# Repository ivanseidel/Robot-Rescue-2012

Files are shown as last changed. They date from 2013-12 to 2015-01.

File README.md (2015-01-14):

Robot-Rescue-2012
=================

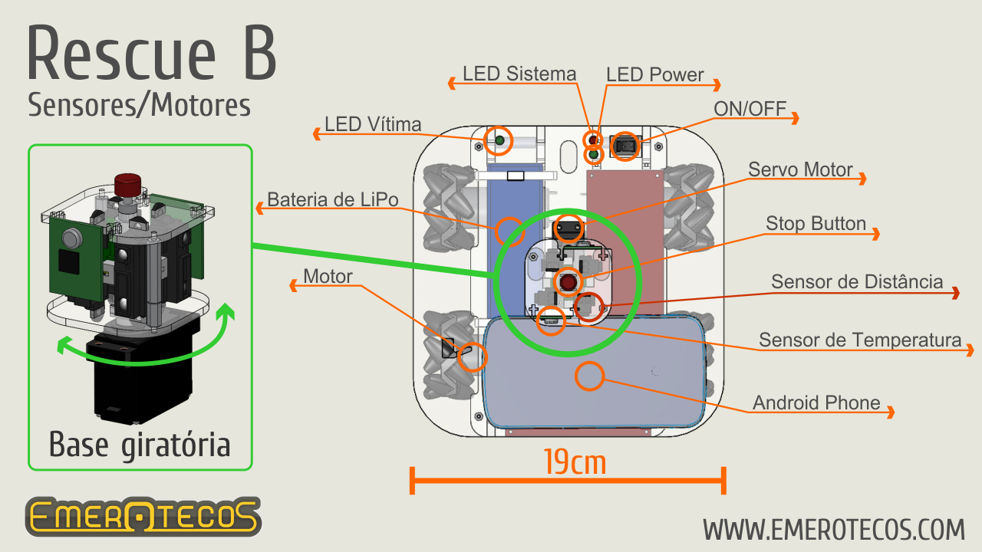
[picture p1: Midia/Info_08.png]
RoboCup Rescue B


This repository includes the entire Rescue B project from 2012, used in the international RoboCup Rescue B league.
Our team could acomplish the 3th place in super-team and 1st place of robot design.

There is a currently new version of it (on the picture, the 2013 one), find out more [here](https://github.com/ivanseidel/Robot-Rescue-2013).

This robot was the first Android based robot, that used the cellphone as the main processor and could controll the entirely the robot. We could acomplish heavy calculations using Android's 2.4Ghz processor, creating really "expensive" euristics.

The software has about 12.000 lines of code, written in Java, using Interfaces, and Classes hierarchy to provide well encapsulated code, and easy to use.

The image bellow is the sketch of the sensors/controllers.

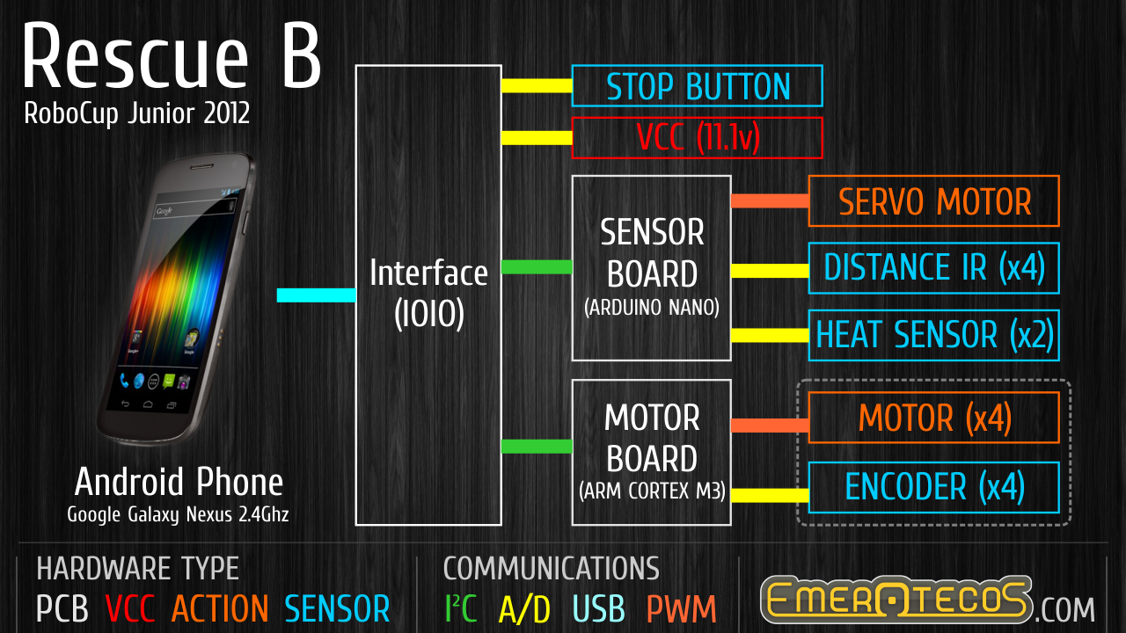
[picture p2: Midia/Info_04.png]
RoboCup Rescue B connections


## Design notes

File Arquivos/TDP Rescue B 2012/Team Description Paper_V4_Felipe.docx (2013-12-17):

[^1]

# Team Description Paper: Team Emerotecos

André Seidel Oliveira¹, Gabriel Lima Guimarães², Ivan Seidel Gomes³, Matheus Pimentel Canejo Pinheiro da Cunha⁴, Hudson Cássio Gomes Oliveira⁵, Felipe Nascimento Martins⁶

Abstract— This paper presents a description of an omnidirectional robot to be used on the Rescue B competition. The main robot controller was written in Java and runs in an Android-based mobile phone. The phone is connected to an IOIO board that serves as an interface between the main controller and the robot’s motors and sensors. The IOIO board connects to an Arduino board, that is responsible for the distance and temperature sensors readings, and to an MBed board that controls the motor drivers. There are four infra-red distance sensors mounted on a rotary base on the top of the robot. The base angle is constantly changed by a servomotor, which allows a 360º distance measuring. The robot mechanical structure was designed using a 3D modeling software and was built using acrylic. It has four omnidirectional wheels that allow the robot to move in any direction without the need of turning itself. The robot was entirely designed, built and programmed by the team students.

# I. Introduction

This is to show team Emerotecos’ strategies to solve the challenge proposed to the Rescue B Competition.

To build the robot, we didn’t use any building kit, as we designed the whole robot from sketch, using Dassault Systemes’ Solid Works software [1]. The robot was built basically with 5mm thick acrylic pieces, whose are tough enough for the application.

As the main processor, we use an Android phone, which is programmed using Java. This is a very interesting platform to work with since nowadays Android is the world’s most popular mobile platform [2].

To send the signals from the Android to the motors (that are controlled by an MBED board [3]), we use a board called IOIO, which is responsible for reading all the sensors as well [4].

# II. Objective

The objective of this project is to build a smart robot that can cross a maze build with wood walls, and identify the electrically heated victims that are placed along the maze’s walls.

# III. Ambient

The Challenge happens in a modular arena, made with wood, which has 2 floors, and 4 main rooms. The location of the walls are always unknown by the time the robot starts running, so that it runs in a real maze. The only constant information about the arena, is its total size, what makes it easier to the robot to find its way on the place. An illustration of the maze is shown in Figure 1.

Some heated “victims” are randomly positioned on some walls in the arena, and the robot has to identify them to get points.

In some places, there are some “dead ends”, which are a black mat on the ground. The robot can run over these black mats, but it has to leave it on the same side it came from, it can’t cross the black area.

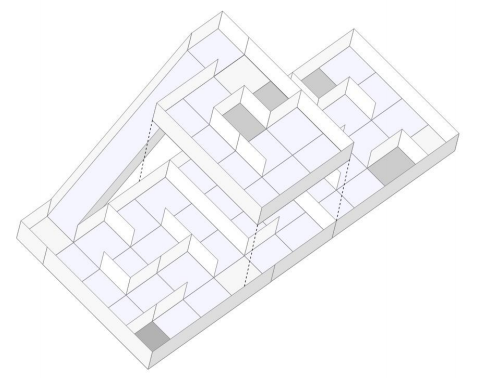
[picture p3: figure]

Figure 1.  Rescue B Arena illustration.

# IV. Strategy

## A. Robot Structure

Our robot is built basically with 2 acrylic layers, and some acrylic beams. We use a Mecanum omnidirectional wheels system, which makes our robot able to drive to every direction. The Mecanum system works as a regular omni system, but it uses 4 tractioned wheels, instead of three, normally used. Figure 2 shows the robot design and Figure 3 shows the actual robot, without the control boards.

We use 4 very strong motors, with encoders, so that we can precisely move our robot everywhere. We rely on 4 motors, one for each wheel, because the MECANUM omnidirectional system need dierent control for each wheel. Each motor can spin giving a 6kgm torque, and its encoder can read up to 3592 pulses per turn because we have a 75:1 speed reduction.

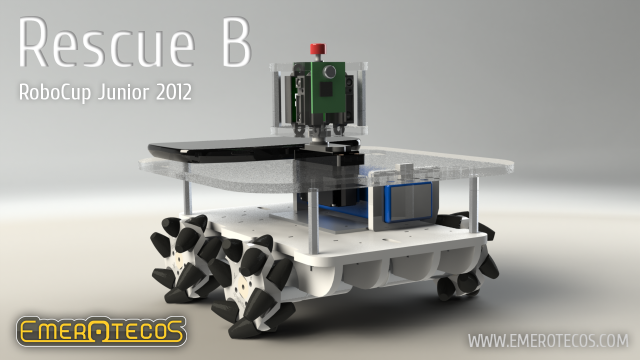
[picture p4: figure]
Info_05

Figure 1.  Robot design.

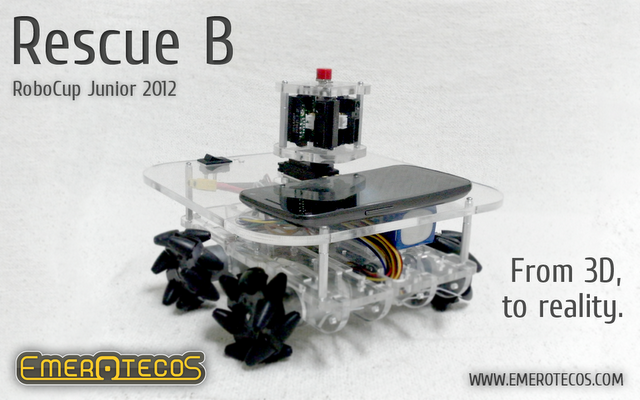
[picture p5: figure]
Info_06

Figure 2.  Robot picture(without control boards).

To process the encoder pulses, we have a MBED board, using a ARM Cortex M3, at 100MHz. This board is also responsible for controlling the engines speed. The communication protocol used to read the encoders from the interface, and to set the motors speeds, is the I²C. The MBED board only has 3 encoder inputs. So, we had to program another encoder counter.

To make good measurements with the infrared distance sensors, we’ve put them in a turnable head over the robot, so that we can make meausures to every direction. To identify the victims, we have 4 thermal infrared sensors strategically positioned around the robot, so that we can measure temperatures in every wall.

As we use complex algorithms (described latter), we need a very complex processing unit. For this reason we have decided to use an Android phone on our robot. Android because we can program using Java. Also, the phone has a touchscreen LCD screen and several sensors we can access. For instance, we make use of the 3 axles gyroscope and 3 axles magnetometer that are present on the Android phone. This gives the robot a very precise way to know it’s position and angle, on all axles.

As you can see in the Figures 2 and 3, the distance sensors are positioned on rotary base on the top of the robot. This base is driven by a servomotor so that the sensors can be aimed to virtually any direction. Its visible too how are the Mecanum wheels mounted on the robot, similar to a Four by Four car, but with the capacity of moving to any direction without the need to turn.

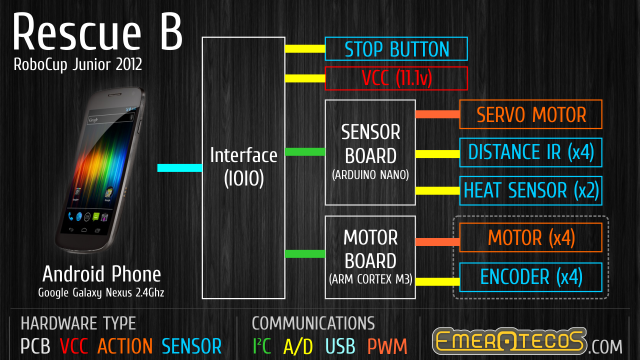
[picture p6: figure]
Info_04

Figure 3.  Control System overview.

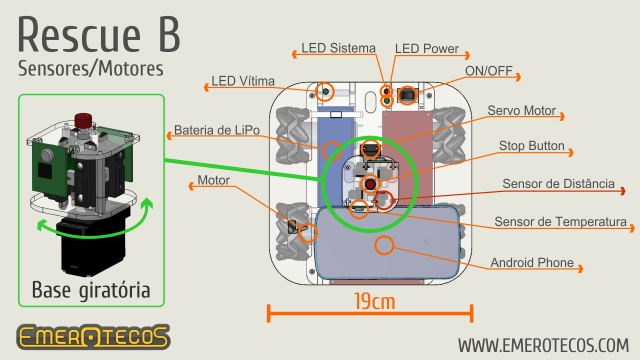
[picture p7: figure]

Figure 4.  Rotary base (left) and top view of the robot.

## B. Programming

The main controller of our robot is an Android cellphone. We choose Android, because it’s an open platform [2], and it’s possible to connect the cellphone with the sensors easily, using the IOIO board [4].

The Android phone sends and receives data to/from the IOIO, which reads the sensors, and communicates with the MBED board, the one responsible for controlling the motors. Figure 4 shows the control system overview.

Our robot uses 2 types of sensors: infrared distance sensor (by Sharp) and heat sensor. The heat sensor is used to detect the victims and are placed on the robot borders. As explained on the previous section, the infrared sensors are mounted on a rotary base. Each one of infrared sensors are pointed 90º from each other in a way that the 4 distance measures can be made at once. The 4 distance measures are repeated several times during a head rotation (one measure per degree) in order to detect the maze walls and obstacles. Figure 5 shows the rotary base with the infrared sensors placed on it, and presents a top view of the robot.

The distance measures are also used to correct the robot alignment in order to maintain its correct orientation parallel to the maze walls. This is done by comparing the measures at 20º and -20º from the central line, and calculating the necessary robot turning to make the robot alignment. Figure 6 illustrates the described idea.

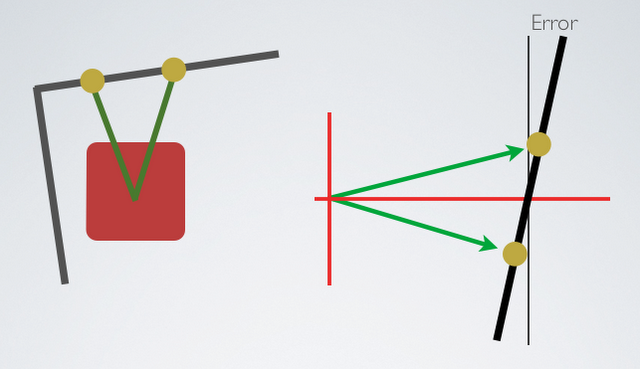
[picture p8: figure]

Figure 5.  Robot design.

To move the robot, we use a simplified kind of SLAM (Simultaneous Localization And Mapping) algorithm, so that we can map the arena. We know that the walls are oriented in only 2 directions (0º and 90º), and we also know that each part of the maze is formed by a 30 x 30 cm square. With this knowledge and using the distance measures obtained via the infrared sensors, we can find out the walls positions and build a map of the maze. The SLAM was programmed in JAVA, and it runs on the Android while the robot is moving in the arena.

While the robot walks around the arena, we can see the map being formed on the cellphone’s screen. Figure 6 shows an example of the mapping screen.

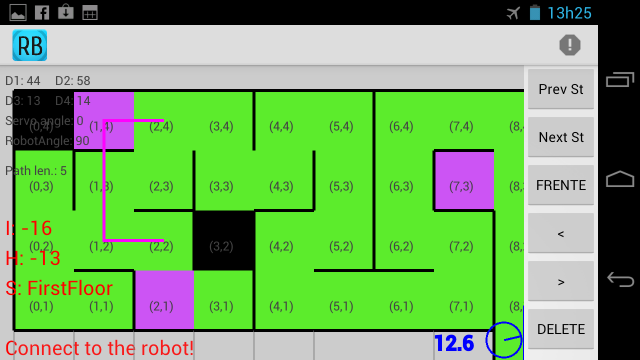
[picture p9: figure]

Figure 6.  On-line mapping.

# V. Conclusion

Mapping is the best way to solve this challenge, because it makes it easy to visit every module of the arena, and consequently, find all victims. We have successfully used this robot in the RoboCupJunior 2012 Rescue B competition. A presentation video about the robot is available in [5].

# VI. Acknowledgement

The authors thank the following companies for the financial support that allowed the robot construction and participation at the 2012 RoboCup and CBR competitions: Proesi Componentes Eletrônicos, Nova Didacta, InTechno Desenvolvimento e Capacitação, Copy Express, Produtiva Hailtools, Use Móveis para Escritórios and Qualidata. They also thank IFES for the support and FAPES (a foundation of the Secretary of Science and Technology of the State of Espirito Santo, Brazil) for the financial support to pay for the air tickets and travel expenses to Fortaleza – LARC 2012 (Project 57768773/2012).

# References

[1] 3D CAD Design Software SolidWorks. Available at: http://www.solidworks.com/. Access: Sep. 5, 2012.
[2] Andoid, the world’s most popular mobile platform. Available at: http://developer.android.com/about/index.html. Access: Sep. 5, 2012.
[3] Mbed - Rapid Prototyping for Microcontrollers. Available at: http://mbed.org/. Access: Sep. 5, 2012.
[4] IOIO Documentation. Available at: https://github.com/ytai/ioio/wiki. Access: Sep 5, 2012.
[5] NERA. Prêmio de Melhor Robô do mundo é de alunos do IFES! (com vídeo). Available at http://nera.sr.ifes.edu.br/?p=143. Access: Sep. 5, 2012.

[^1] The authors are with the Federal Institute of Education, Science and Technology of Espírito Santo (IFES). Rodovia ES-010, km 6,5 - Manguinhos, Serra, ES. andre_oliveira@live.com¹, gablg@hotmail.com², ivanseidel@gmail.com³, pimentelcanejo@hotmail.com⁴, hudsoncassio@ifes.edu.br⁵, felipemartins@ifes.edu.br⁶.

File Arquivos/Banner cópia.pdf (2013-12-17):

## The Problem

One of our biggest problems is to find all victims in the maze, the fastest way possible. As we don’t have to find the end of the maze, to find all victims, all we have to do is go everywhere in the maze.

## The Robot: Mechanics

This year, we said bye to the NXT brick, thanks to it’s weight, and to it’s engines size. We decided to build from sketch an entire robot, using 2 5mm acrylic layers and some acrylic beams under the structure to support the engines and the electronics. The MECANUM wheels, are just like an ordinary omnidirectional system, but with the wheel mounted in a different way.
We use a servo in the center of the robot, that is used to move the sensors, giving them a bigger reading area.
Our robot measures 200x200mm, which makes it possible for the robot to spin without touching the walls. We use 5mm acrylic, because we know (by tests) that it is tough enough. We cut it with laser (on CopyExpress) giving us a 0.01cm precision. All drawing have been made on SolidWorks!
We also used a 3D printer to do some parts on our robot, like the thermopile array`s stand.

## The Robot: Electronics

Yes, we use a cellphone! As we use very complex algorithms, we need a very complex processing unit, that’s why there is an Android phone on our robot. Android because we can program using java, without any problem, and we still have a LCD screen, and a touchscreen panel, with which we can make the initial configurations.
To fire up the engines, read the sensors, and control the engines position, we have, basically 2 PCB’s.
To feed the monster, we use a liPo battery, which gives us 11.1v, 65A, and is very lightweight.

### Interface

We have a interface that is responsible to connect the Android (via USB) to the robot. It`s called the IOIO board, which will communicate with the MBED, that will read the sensors and spin the wheels.

### Locomotion

We rely on 4 engines, one for each wheel, because the MECANUM omnidirectional system need different control for each wheel. Each engine can spin giving a 6kg torque, and can read up to 3592 pulses per turn of the final axle even though we have a 75:1 speed reduction.
To process all this pulses, we have a MBED board, using a ARM Cortex M3, at 100Mhz speed. That board is also responsible for controlling the engines speed. The protocol used to read the encoders from the interface, and to set the speeds, will be I2C Fast.
The MBED board have an onboard encoder counter for only 3 engines, fact that make us emulate another encoder counter (he hope NXP can read this, so that, on the next time, we won’t need to emulate the counter)

### Sensoring

The Algorithm we’re using needs a lot of distance measures around the robot. If one rotates 4 sensors for 90 degrees, one’ve got 360 degrees of pure distance measurement! And as we use 2 thermopiles arrays, one’ll have a 180 degrees of temperature measurement (more than enough).
The MBED is responsible for making the reading, filtering, and sending them via I2C!

### IMU

Besides all that sensors, we also have an 9 axles Inertial Measurement Unit (IMU). It’s basically an unit that joins a 3 axles gyroscope, a 3 axles accelerometer, and a 3 axles magnetometer, giving the robot a very precise way to know it’s position and angle, on all axles (we hope we are in a 3D world).

## The Robot: Software

We will do our best to find the victims the fastest we can. We’re used to write all the code in C, but this time, we are using C++ for the MBED and Java (and C++) for the Android. This year, we`re implementing a very complex algorithm, usually used in situations involving mazes. It`s called SLAM! (simultaneous localization and mapping). As you can see, the algorithm basically maps the arena, but in the same time, it locates the robot in the arena.

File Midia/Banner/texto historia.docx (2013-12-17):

O império Bizantino foi um império formado por várias nações da Eurásia como continuação do império Romano do Oriente durante o fim da Antiguidade Tardia e a Idade Média, a partir do século IV, depois da tomada do império Romano do Ocidente pelas invasões bárbaras.

A história desse império se inicia com a dinastia de Constantino I, que mudou a sede do Império para sua recem-fundada cidade Constantinopla no ano de 330. O principal motivo para essa mudança repentina foram os constantes ataques bárbaros ao lado Ocidental do Império Romano.

Sob o domínio de Constantino I, Roma teve grandes mudanças, sendo as principais a popularização do cristianismo e a valorização da moeda, que levou o Império a se tornar próspero novamente e, consequentemente, a re-estruturar seu exército.

O estado do império até os anos de 400 pode ser descrito em termos do resultado do trabalho de Constantino. O princípio dinástico foi estabelecido tão firmemente que o imperador que morreu naquele ano, Teodósio I, deixou o cargo imperial em conjunto para seus filhos: Arcádio no Oriente e Flávio Honório no Ocidente. Teodósio foi o último imperador a governar o Império Romano único.

O império do Oriente foi poupado das dificuldades enfrentadas pelo Ocidente nos séculos III e IV, em parte devido a uma cultura mais urbana e mais recursos financeiros que lhe permitiu aplacar invasões com tributos e o pagamento de mercenários estrangeiros. Teodósio II fortaleceu as muralhas de Constantinopla, construindo o Muro de Teodósio (408-413),deixando a cidade imune a maioria dos ataques. Os muros não foram violados até 1204. A fim de afastar os hunos, Teodósio prestava-lhes tributos.

O sucessor de Teodósio, Marciano, se recusou a continuar a pagar essa quantia exorbitante.Por essa altura, no entanto, Átila já havia desviado sua atenção para o Império Romano do Ocidente. Após sua morte em 453, seu império desmoronou e Constantinopla iniciou um relacionamento rentável com os hunos restantes, que acabaram lutando como mercenários do exército bizantino.

Após a queda de Átila, o Império do Oriente viveu um período de paz, enquanto o Império Romano do Ocidente continuou sua lenta agonía (seu fim é geralmente datado em 476, quando o general romano-germânico Odoacro depôs o imperador titular do ocidente Rômulo Augusto).

A partir do ano de 533 os Bizantinos começaram seu processo de expansão, principalmente para retomar a área ocidental do antigo Estado Romano. As conquistas ocidentais começaram com Justiniano enviando seu general Belisário para recuperar a antiga província da África Proconsular dos vândalos, que tinha estado no controle deles desde 429 com sua capital em Cartago. Seu sucesso veio com uma facilidade surpreendente, mas apenas em 548 as tribos locais foram subjugadas. Na Itália dos ostrogodos, a morte de Teodorico, o Grande, seu sobrinho e herdeiro Atalarico, e sua filha Amalasunta havia deixado seu assassino Teodato no trono, apesar de sua autoridade enfraquecida. Em 535, uma pequena expedição bizantina na Sicília foi cumprida com fácil sucesso, mas os godos logo endureceram a sua resistência e a vitória não veio até 540, quando Belisário capturou Ravena, após o cerco de sucesso de Nápoles e Roma.

Os ostrogodos unidos sob o comando do rei Totila capturaram Roma em 17 de dezembro de 546. Justiniano, mais tarde, chamou Belisário de volta para Constantinopla no início de 549 de Ravena. A chegada do eunuco armênio Narses na Itália (final de 551) com um exército de cerca de 35.000 homens marcou outra mudança na sorte gótica. Totila foi derrotado na Batalha de Busta Gallorum e seu sucessor, Teia, foi derrotado na Batalha de Mons Lactarius (outubro de 552). Apesar da resistência contínua a partir de algumas guarnições góticas e duas invasões subsequentes pelos francos e alamanos, a guerra na península Itálica estava no fim. Em 551, Atanagildo, um nobre visigodo da Hispânia procurou a ajuda de Justiniano em uma rebelião contra o rei, e o imperador enviou uma força sob Libério, um comandante militar de sucesso. O império bizantino manteve uma pequena fatia do litoral da Espanha até o reinado de Heráclio.

No leste, as Guerras romano-persas prosseguiram até 561, quando Justiniano e emissários de Cosroes chegaram a um acordo sobre uma paz de 50 anos. Em meados dos anos 550s, Justiniano teve vitórias na maioria dos teatros de operação, com a notável exceção dos Bálcãs, que foram submetidos a repetidas incursões dos eslavos. Em 559, o império enfrentou uma grande invasão dos kutrigurs e sclaveni. Justiniano chamou Belisário de seu retiro e ele derrotou os novos hunos. O reforço das frotas do Danúbio causou a retirada dos kutrigurs e eles concordaram em um tratado que permitiu a passagem segura para o outro lado do Danúbio.

Após Justiniano morrer em 565, seu sucessor, Justino II se recusou a pagar o grande tributo para os persas. Enquanto isso, os lombardos invadiram a península Itálica; até o final do século, apenas um terço da Itália estava nas mãos dos bizantinos. O sucessor de Justino II, Tibério II, escolhendo entre seus inimigos, atribuiu subsídios aos ávaros ao tomar uma ação militar contra os persas. Embora o general de Tibério II, Maurício, tenha liderado uma campanha eficaz na fronteira oriental, os subsídios não conseguiram conter os ávaros. Eles capturaram nos Bálcãs a fortaleza de Sirmium em 582 d.C., enquanto os eslavos começaram a fazer incursões sobre o Danúbio. Maurício, que sucedeu Teodósio, interveio em uma guerra civil persa colocando o legítimo Cosroes II de volta ao trono e casou sua filha com ele. O tratado de Maurício com seu genro trouxe um novo status territorial para o leste, alargando as fronteiras a uma extensão nunca antes alcançada pelo império em sua história além de ser muito barato defender as fronteiras durante esta nova paz perpétua – milhões de soldos foram economizados pela remissão de tributo aos persas. Após esta vitória sob a fronteira oriental, Maurício era livre para se concentrar nos Bálcãs e por 602 após uma série de campanhas bem sucedidas ele empurrou os ávaros e eslavos de volta sobre o Danúbio.

A partir de 649, os árabes começaram a fazer ataques navais contra o império chegando a controlar Chipre. Os árabes, já firmemente controlando a Síria e o Levante, enviaram frequentes incursões às profundezas da Anatólia, e entre 674 e 678 fizeram um cerco a Constantinopla. A frota árabe foi firmemente repelida através do uso do fogo grego, e uma trégua de trinta anos, foi assinada entre o império bizantino e o califado omíada. As incursões da Anatólia permaneceram inabaladas, e acelerou o fim da cultura urbana clássica, com os habitantes de muitas cidades, quer refortificando áreas muito menores no interior das muralhas da cidade velha, ou se mudando totalmente as fortalezas próximas. Constantinopla caiu consideravelmente em tamanho, de 500.000 habitantes a apenas 40.000-70.000, como a cidade perdeu o embarque livre de grãos em 618 após a derrota do Egito para os persas (a província foi recuperada em 629, mas foi perdida para os invasores árabes em 642). O vazio deixado pelo desaparecimento das velhas instituições cívicas semi-autônomas foi preenchido pelo sistema de themas, o que implicou a divisão da Anatólia em "províncias" ocupadas por exércitos distintos, que assumiram a autoridade civil e responderam diretamente ao governo imperial. Este sistema pode ter tido suas raízes em determinadas medidas pontuais adotadas por Heráclio, mas ao longo do século VII se transformaram em um sistema totalmente novo de governo imperial.

A retirada de um grande número de tropas dos Bálcãs para combater os persas e os árabes no Oriente abriu as portas para a expansão gradual dos povos eslavos do sul para a península e, como na Anatólia, muitas cidades caíram para pequenos povoados fortificados.[72] Nos anos 670s, os búlgaros foram empurrados do sul do Danúbio com a chegada dos cazares, e em 680 forças bizantinas que tinham sido enviadas para dispersar esses novos assentamentos foram derrotadas. No ano seguinte, Constantino IV assinou um tratado com o Khan búlgaro Asparukh, e o Império Búlgaro assumiu a soberania sobre certo número de tribos eslavas que, anteriormente, pelo menos nominalmente, reconheceram a soberania bizantina. Em 687-688, o imperador Justiniano II liderou uma expedição contra os eslavos e os búlgaros, obtendo ganhos significativos, embora o fato de que ele teve que lutar no seu caminha da Trácia a Macedônia demonstra o grau em que o poder bizantino na região norte dos Bálcãs havia diminuído.

A partir de 700 o Império Bizantino participou de várias guerras por território, mas sempre mantendo a integridade de sua capital, Constantinopla. Depois de muitos anos de guerras de expansão e defendendo suas fronteiras, em 1200 Constantinopla começou a ser seriamente ameaçada e o Império Bizantino deu seus primeiros sinais de enfraquecimento. O movimento cruzadista e a ascensão comercial das cidades italianas foram responsáveis pela desestruturação do Império. No século XIV, a expansão turco-otomana na região dos Bálcãs e da Ásia Menor reduziu o império à cidade de Constantinopla. Finalmente, em 1453, os turcos dominaram a cidade e deram o nome de Istambul, uma das principais cidades da Turquia.

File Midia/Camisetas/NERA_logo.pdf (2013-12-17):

# NER@

Núcleo de Estudos em Rob Núcleo de Estudos em Rob úcleo de Estudos em Robótica e Automaç ótica e Automaç ótica e Automação- IFES

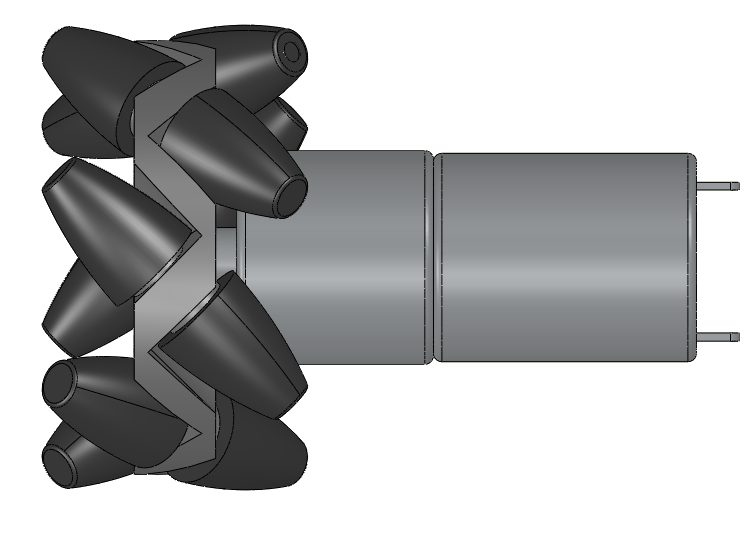
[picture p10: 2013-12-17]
Software/Android/Img/motor_large.png

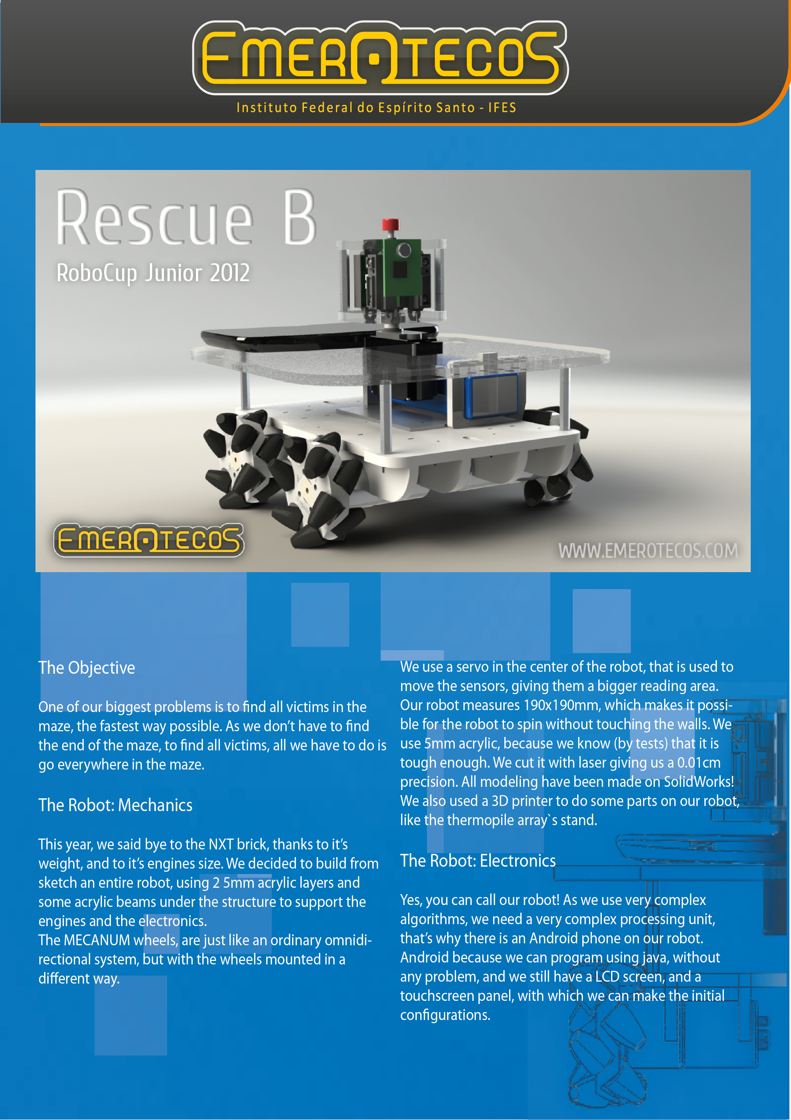
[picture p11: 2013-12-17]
Arquivos/Frente_01.png

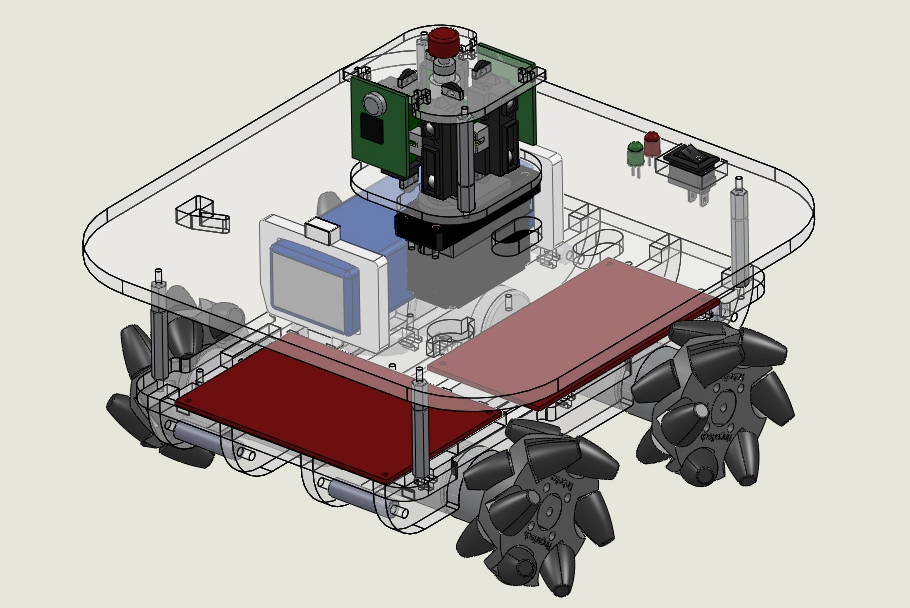
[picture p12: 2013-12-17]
Midia/Robo_04.JPG

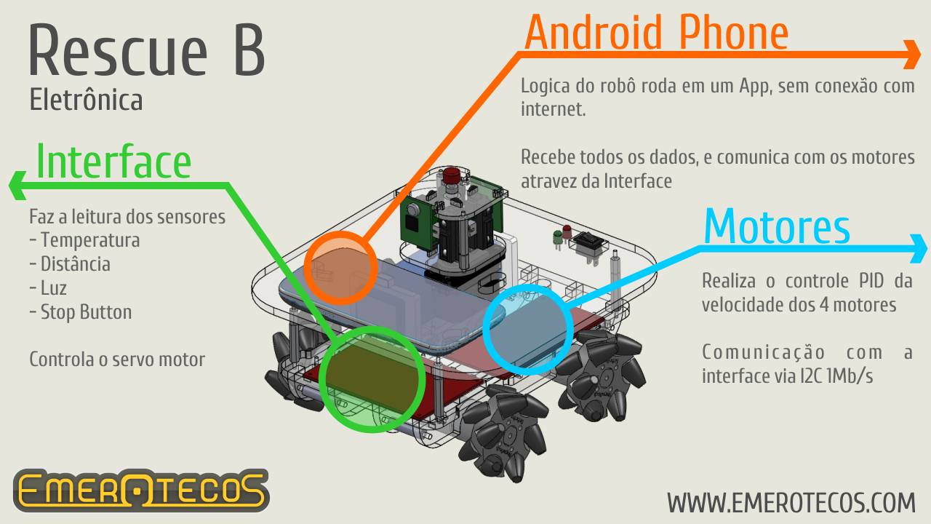
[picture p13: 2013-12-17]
Midia/Info_07.png

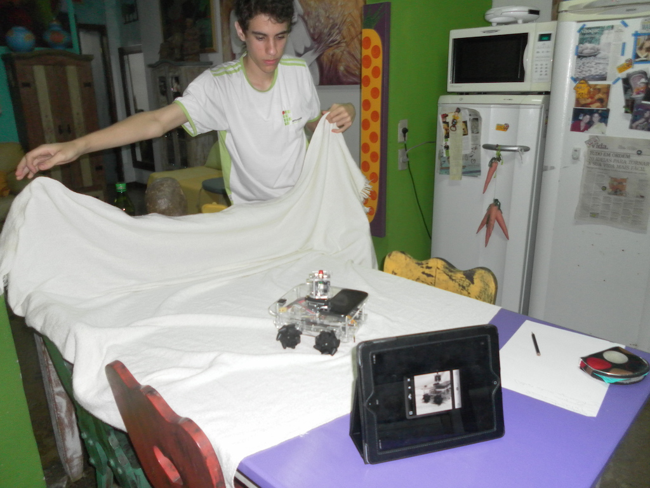
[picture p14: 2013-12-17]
Midia/Fotos/SAM_9522.JPG

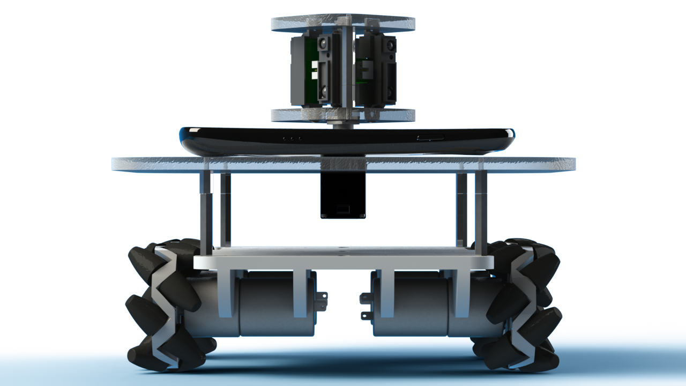
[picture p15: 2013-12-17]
Midia/Render_07.png

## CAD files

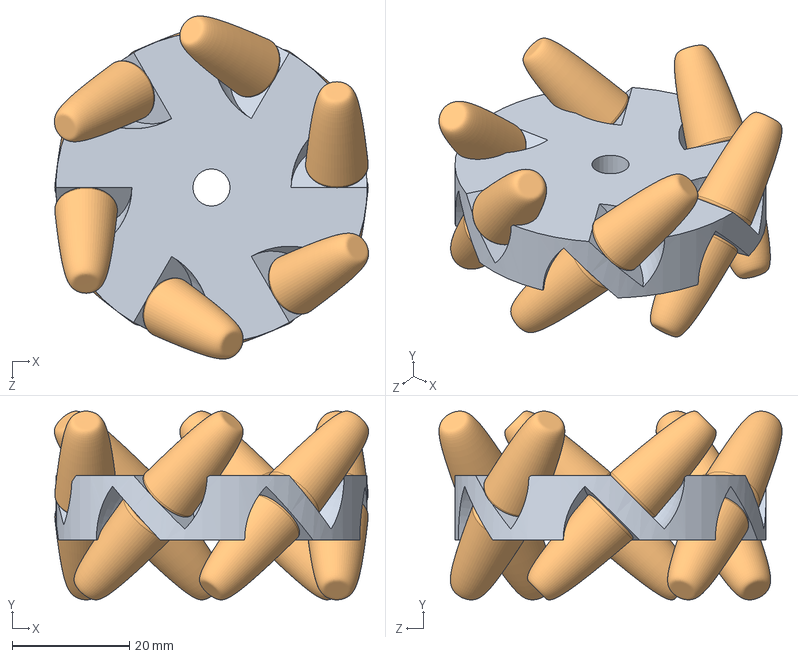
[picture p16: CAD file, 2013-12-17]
Mecanica/Partes/Mecanum.SLDASM
53.7 x 32.3 x 58.6 mm
Mecanum_meio
Mecanum_wheel x 12

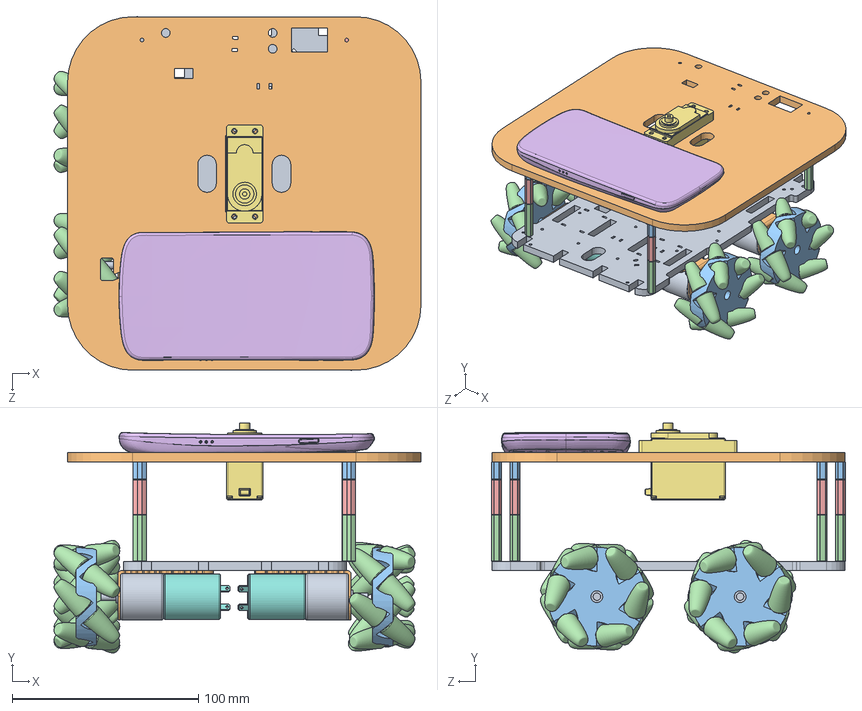
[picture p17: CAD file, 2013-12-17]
Mecanica/Robo_01.SLDASM
197.3 x 123.6 x 190.5 mm
Plataforma_1
Plataforma_2
PC-Standoff - 9.5mm - FF x 4
PC-Standoff - 25mm x 4
PC-Standoff - 19mm x 4
Nexus
Servo-HS-311
Motor x 4
Motor_Redutor x 4
Suporte_Motor x 4
Mecanum_meio x 4
Mecanum_wheel x 48

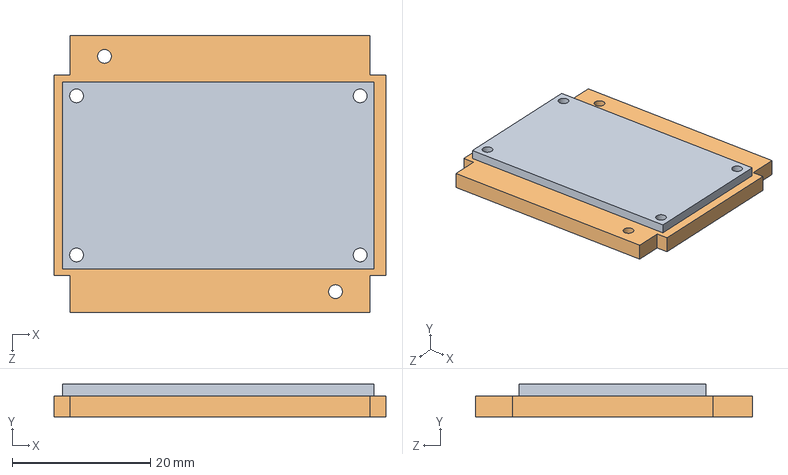
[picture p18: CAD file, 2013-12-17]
Mecanica/Sensor_luz.SLDASM
48.0 x 4.70 x 40.0 mm
Sensor_luz
Base_sensor_luz

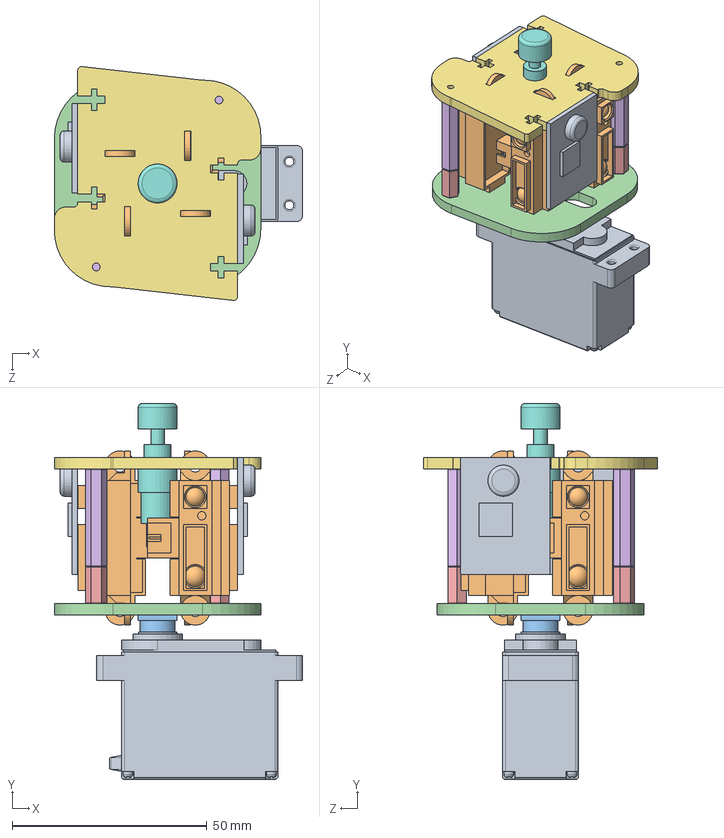
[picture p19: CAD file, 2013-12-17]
Mecanica/Sensores.SLDASM
63.7 x 96.4 x 60.0 mm
Servo-HS-311
Sharp_ir_sensor x 4
Servo_horn
Base_sensores_1
PC-Standoff - 9.5mm - FF x 2
PC-Standoff - 25mm x 2
Base_sensores_2
Push_button_1
sensor_temperatura x 2

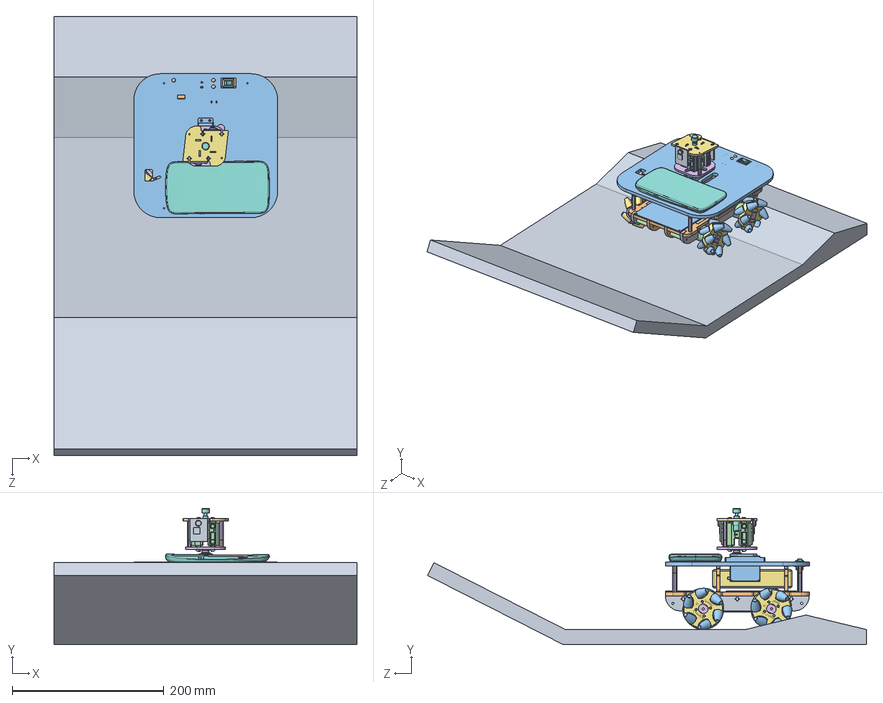
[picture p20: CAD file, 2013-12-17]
Mecanica/Robo_02.SLDASM
400.0 x 180.1 x 579.6 mm
Plataforma_1
Plataforma_2
PC-Standoff - 25mm - FF x 4
PC-Standoff - 9.5mm - FF x 6
PC-Standoff - 25mm x 6
bateriaLiPO
Nexus
viga_motor_1 x 2
viga_motor_2 x 2
Motor x 4
Motor_Redutor x 4
Encoder x 4
Mecanum Hub Mirrored B R2 x 2
rubber roller_1 x 24
steel pin_1 x 12
Flat Washer Type A Narrow_AI_FW 0.125_1 x 24
Mecanum mount R2_1 x 2
rubber roller x 24
steel pin x 12
Flat Washer Type A Narrow_AI_FW 0.125 x 24
Mecanum mount R2 x 2
Mecanum Hub A R2 x 2
Switch_KCD11
LED_green x 2
LED_red
Servo-HS-311
Sharp_ir_sensor x 4
Servo_horn
Base_sensores_1
Base_sensores_2
Push_button_1
sensor_temperatura x 2
Suporte_bateria_1 x 2
Interface
Sensor_luz
Base_sensor_luz
Motores

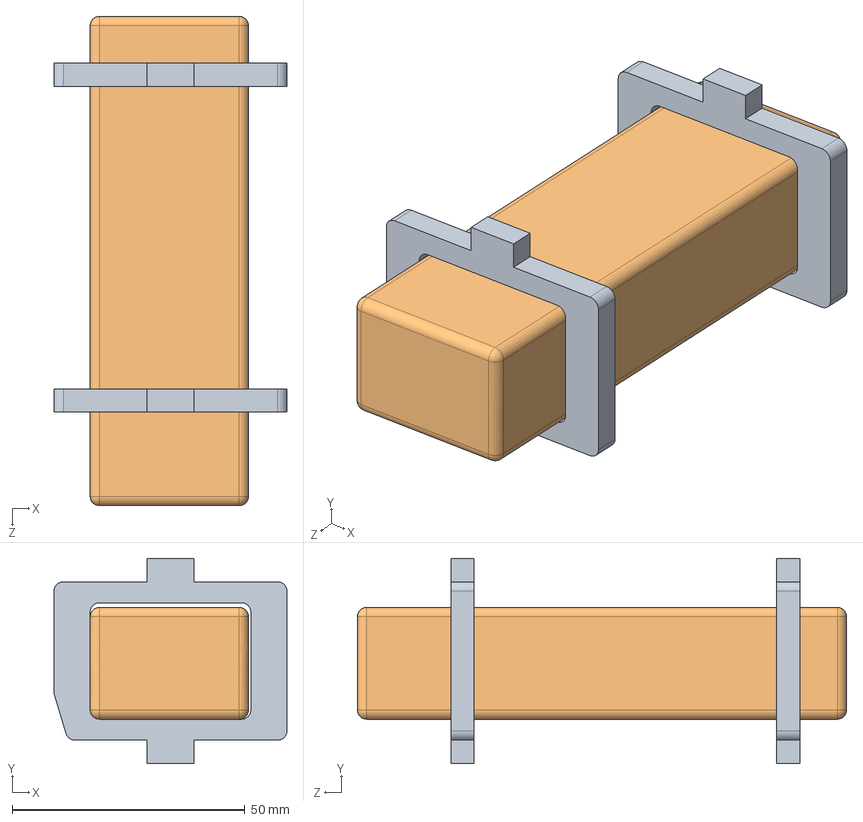
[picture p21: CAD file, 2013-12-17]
Mecanica/Bateria_suportes.SLDASM
50.0 x 44.0 x 105.0 mm
Suporte_bateria_1 x 2
bateriaLiPO

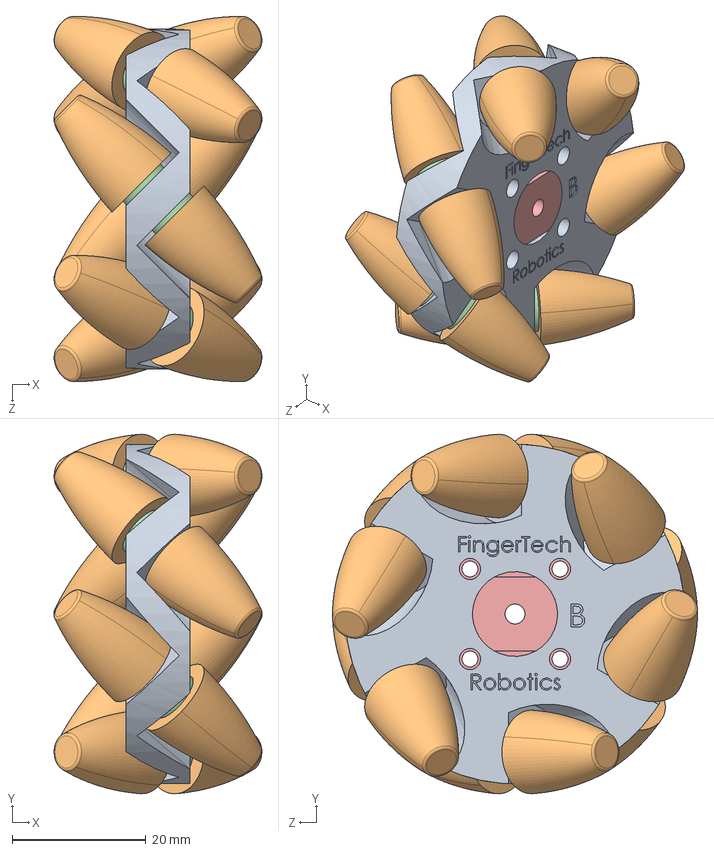
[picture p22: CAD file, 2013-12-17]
Mecanica/Partes/Mecanum Wheel B.SLDASM
31.1 x 53.8 x 54.6 mm
Mecanum Hub Mirrored B R2
rubber roller x 12
steel pin x 6
Flat Washer Type A Narrow_AI_FW 0.125 x 12
Mecanum mount R2

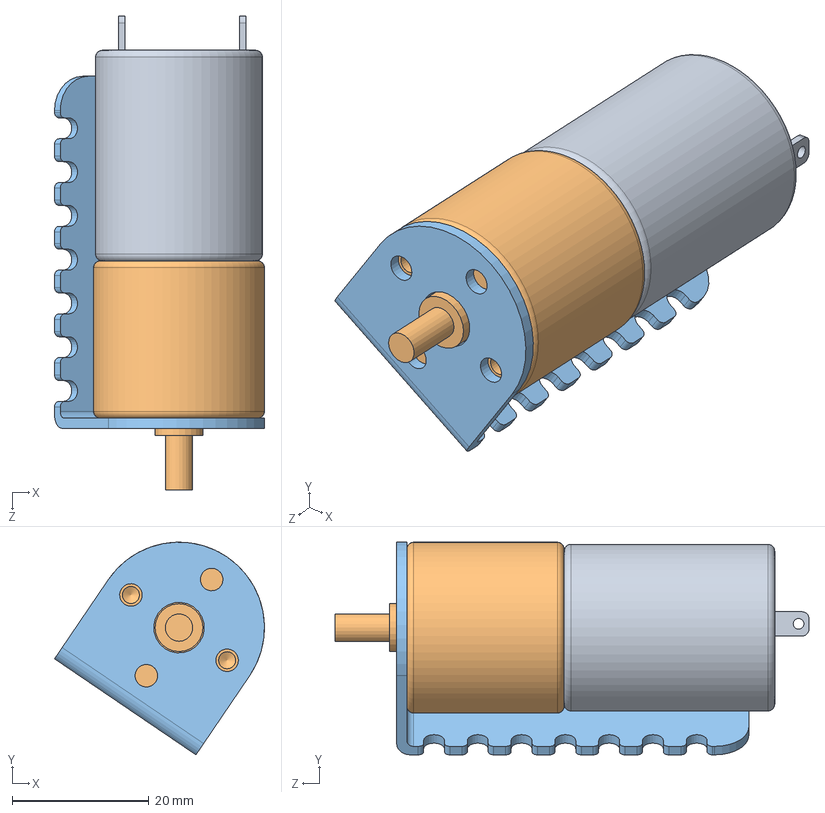
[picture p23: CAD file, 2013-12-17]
Mecanica/Partes/Motor_com_suporte.SLDASM
30.7 x 31.1 x 69.3 mm
Motor
Motor_Redutor
Suporte_Motor

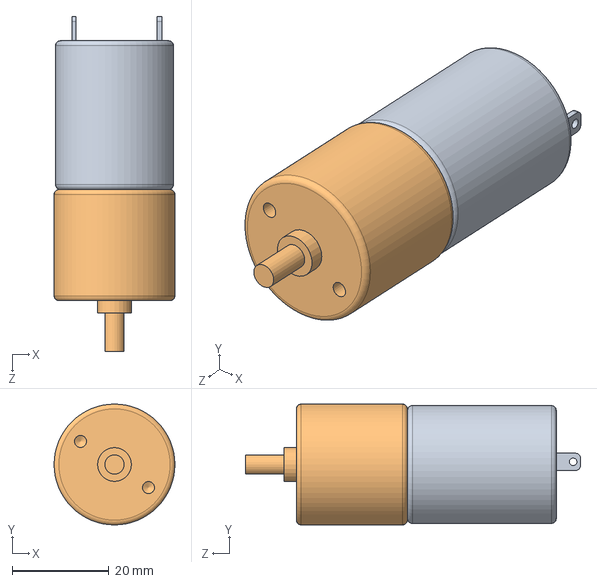
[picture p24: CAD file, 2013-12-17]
Mecanica/Partes/Motor.SLDASM
25.0 x 25.0 x 69.3 mm
Motor
Motor_Redutor

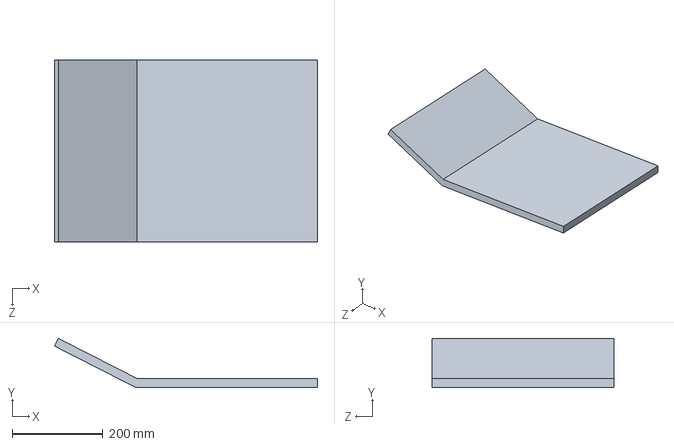
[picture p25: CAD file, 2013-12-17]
Mecanica/Ambiente/Rampa.SLDPRT
579.6 x 108.4 x 400.0 mm

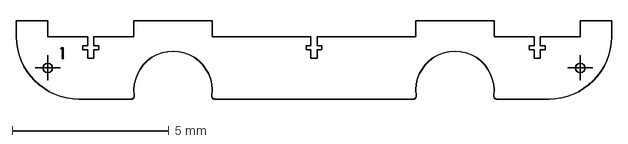
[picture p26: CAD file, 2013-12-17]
Mecanica/Corte_laser_01/viga_motor_1.DXF
19.0 x 2.50 mm

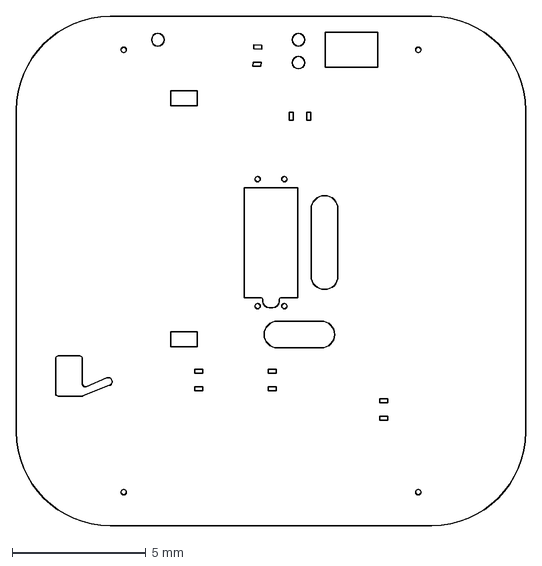
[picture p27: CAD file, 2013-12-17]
Mecanica/Corte_laser_03/Plataforma_2.DXF
19.0 x 19.0 mm

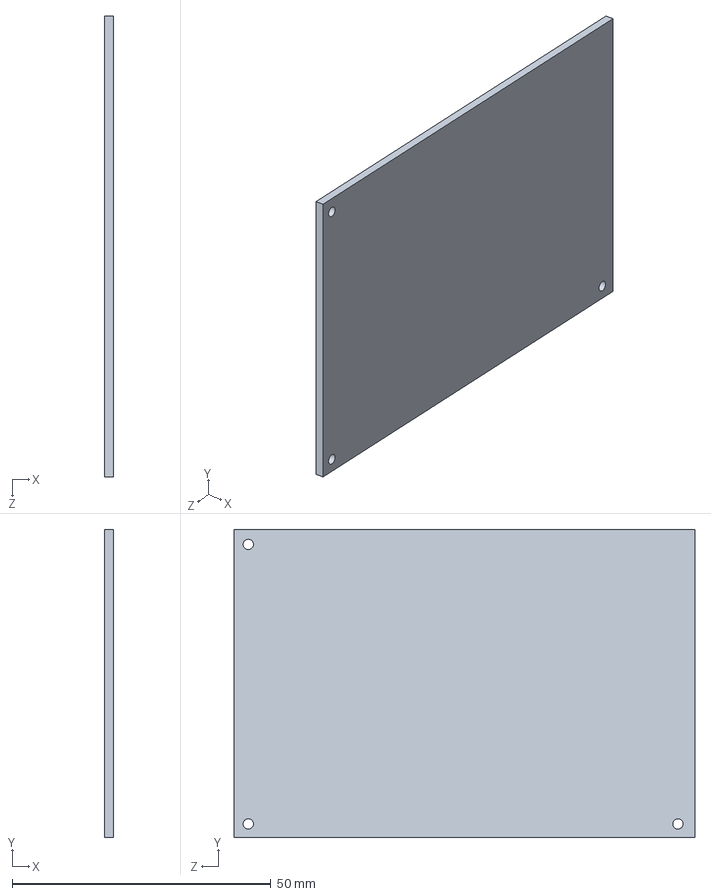
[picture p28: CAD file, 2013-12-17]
Mecanica/Eletronica/Interface.SLDPRT
1.66 x 59.5 x 89.0 mm

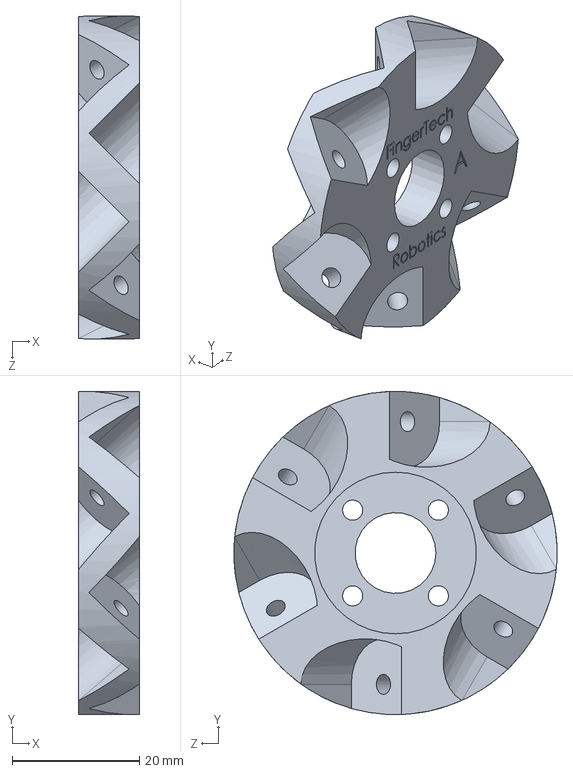
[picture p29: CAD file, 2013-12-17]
Mecanica/Partes/Mecanum Hub A R2.sldprt
9.53 x 50.8 x 50.7 mm

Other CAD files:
Mecanica/Partes/Mecanum Wheel A.SLDASM
Mecanica/Corte_laser_02/viga_motor_2.dxf
Mecanica/Output/Plataforma_2.DWG
Mecanica/Suporte_bateria_1.SLDPRT
Mecanica/Base_sensor_luz.SLDPRT
Mecanica/Base_sensores_1.SLDPRT
Mecanica/Base_sensores_2.DXF
Mecanica/Base_sensores_2.SLDPRT
Mecanica/Corte_laser_01/Base_sensores_1.DXF
Mecanica/Corte_laser_01/Base_sensores_2.DXF
Mecanica/Corte_laser_01/Base_sensores_2.SLDDRW
Mecanica/Corte_laser_01/Plataforma_1.DXF
Mecanica/Corte_laser_01/Plataforma_1.SLDDRW
Mecanica/Corte_laser_01/Plataforma_2.DXF
Mecanica/Corte_laser_01/Plataforma_2.SLDDRW
Mecanica/Corte_laser_01/Suporte_bateria_1.DXF
Mecanica/Corte_laser_01/Suporte_bateria_1.SLDDRW
Mecanica/Corte_laser_01/V1.SLDDRW
Mecanica/Corte_laser_01/viga_motor_1.SLDDRW
Mecanica/Corte_laser_01/viga_motor_2.DXF
Mecanica/Corte_laser_01/viga_motor_2.SLDDRW
Mecanica/Corte_laser_02/Base_sensor_luz.DXF
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

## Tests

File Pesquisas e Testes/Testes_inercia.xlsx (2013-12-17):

 | Sem preditor de inercia (Suspenso) | Sem preditor de inércia (Chão) | Com preditor de inércia (Suspenso) | Com preditor (Ré) | 0
0 | 0 | 0 | 0 | 0 | 0 | -3.2443
0.1 | 7 | 8 | 0 | 35 | 3 | 6.4007 | 4877 | 4884
0.15 | 13 | 11 | 2 | 55 | 2 | 11.2232 | 6687 | 6700
0.2 | 16 | 14 | 2 | 69 | -3 | 16.0457 | 8496 | 8512
0.25 | 23 | 22 | 0 | 89 | -1 | 20.8682 | 10309 | 10332
0.3 | 26 | 23 | 5 | 110 | -2 | 25.6907 | 12130 | 12156
0.35 | 31 | 32 | 4 | 133 | 1 | 30.5132 | 13957 | 13988
0.4 | 31 | 37 | 6 | 150 | -4 | 35.3357 | 15785 | 15816
0.45 | 42 | 36 | -1 | 166 | -1 | 40.1582 | 17622 | 17664
0.5 | 53 | 43 | 4 | 186 | -4 | 44.9807 | 19467 | 19520
0.55 | 63 | 50 | 2 | 208 | 1 | 49.8032 | 21325 | 21388
0.6 | 52 | 56 | -5 | 222 | -4 | 54.6257 | 23192 | 23244
0.65 | 63 | 62 | -2 | 241 | 3 | 59.4482 | 25053 | 25116
0.7 | 63 | 62 | -1 | 268 | -6 | 64.2707 | 26921 | 26984
0.75 | 77 | 65 | -2 | 275 | 1 | 69.0932 | 28795 | 28872
0.8 | 82 | 80 | -4 | 293 | -1 | 73.9157 | 30674 | 30756
0.85 | 79 | 82 | 1 | 313 | -6 | 78.7382 | 32561 | 32640
0.9 | 85 | 95 | 6 | 324 | -6 | 83.5607 | 34451 | 34536
0.95 | 99 | 93 | 2 | 345 | -5 | 88.3832 | 36341 | 36440
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

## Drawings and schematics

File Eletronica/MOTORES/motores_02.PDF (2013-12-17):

## MBED1

J1

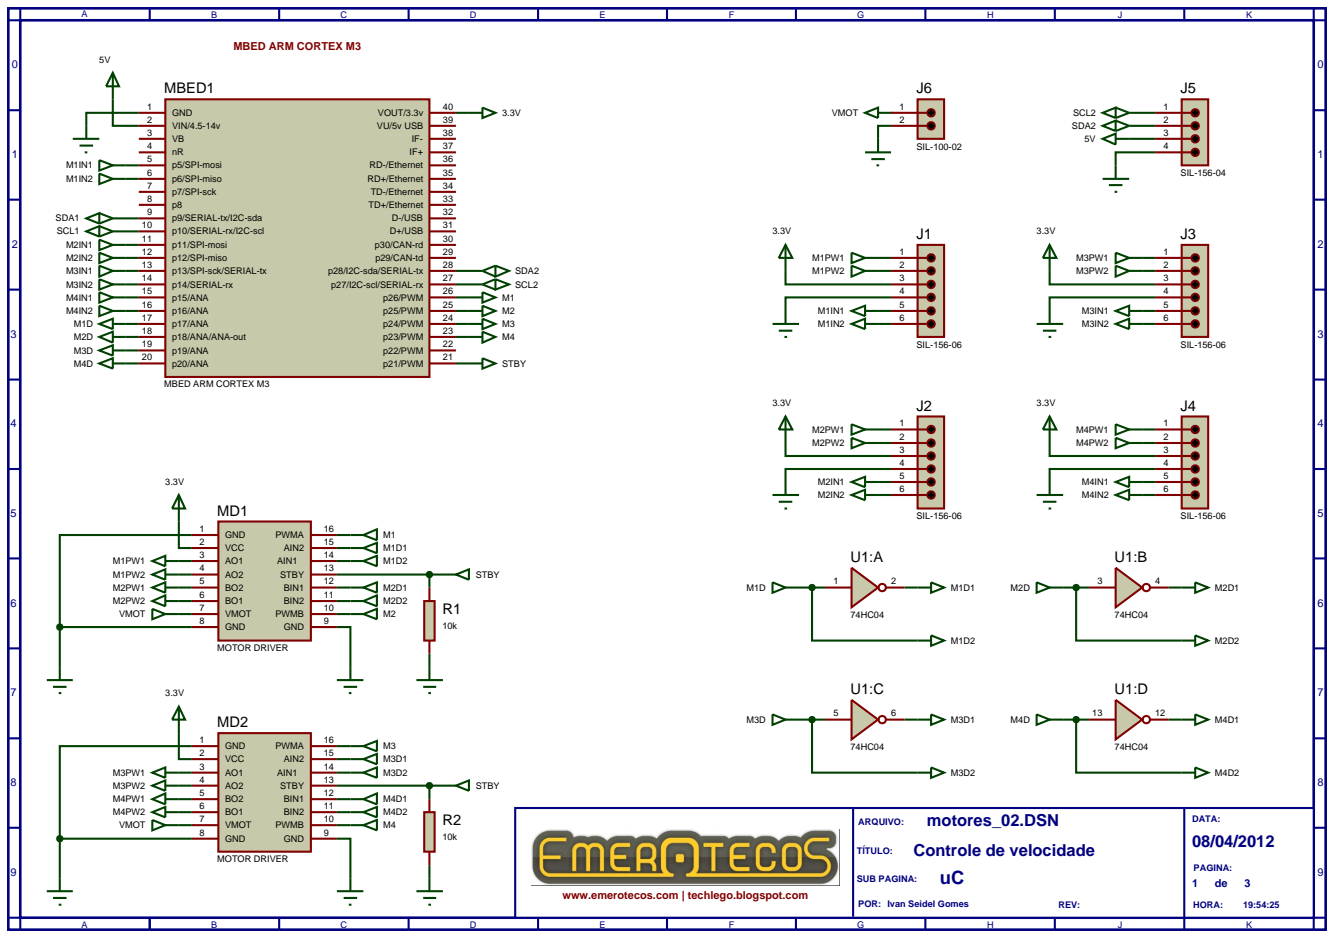
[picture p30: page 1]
ARQUIVO:; POR:; DATA:; PAGINA:; motores_02.DSN; SUB PAGINA:; REV:; HORA:; TÍTULO:; Controle de velocidade; p20/ANA 20; VOUT/3.3v; VU/5v USB; RD-/Ethernet; RD+/Ethernet; TD-/Ethernet; TD+/Ethernet; D-/USB; D+/USB; p30/CAN-rd; p29/CAN-td; p28/I2C-sda/SERIAL-tx; p27/I2C-scl/SERIAL-rx; p26/PWM; p25/PWM; p24/PWM; p23/PWM; p22/PWM; p21/PWM; STBY; SDA1 SCL1; SDA2 SCL2; SIL-156-06; GND 1 VCC 2 AO1 3 AO2 4 BO2 5 BO1 6 VMOT 7 GND 8; PWMA; AIN2; AIN1; BIN1; BIN2; PWMB; GND; MOTOR DRIVER; SIL-156-04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

MBED ARM CORTEX M3

GND 1
VIN/4.5-14v 2
p5/SPI-mosi 5
p6/SPI-miso 6
p7/SPI-sck 7
p9/SERIAL-tx/I2C-sda 9
p10/SERIAL-rx/I2C-scl 10
p11/SPI-mosi 11
p12/SPI-miso 12
p13/SPI-sck/SERIAL-tx 13
p14/SERIAL-rx 14
p15/ANA 15
p16/ANA 16
p17/ANA 17
p18/ANA/ANA-out 18
p19/ANA 19

www.emerotecos.com | techlego.blogspot.com

Ivan Seidel Gomes

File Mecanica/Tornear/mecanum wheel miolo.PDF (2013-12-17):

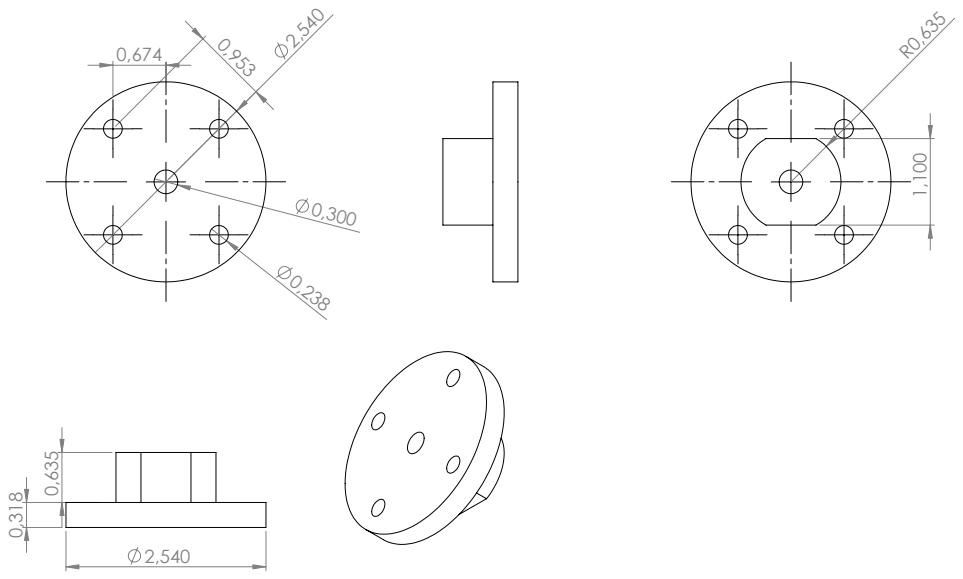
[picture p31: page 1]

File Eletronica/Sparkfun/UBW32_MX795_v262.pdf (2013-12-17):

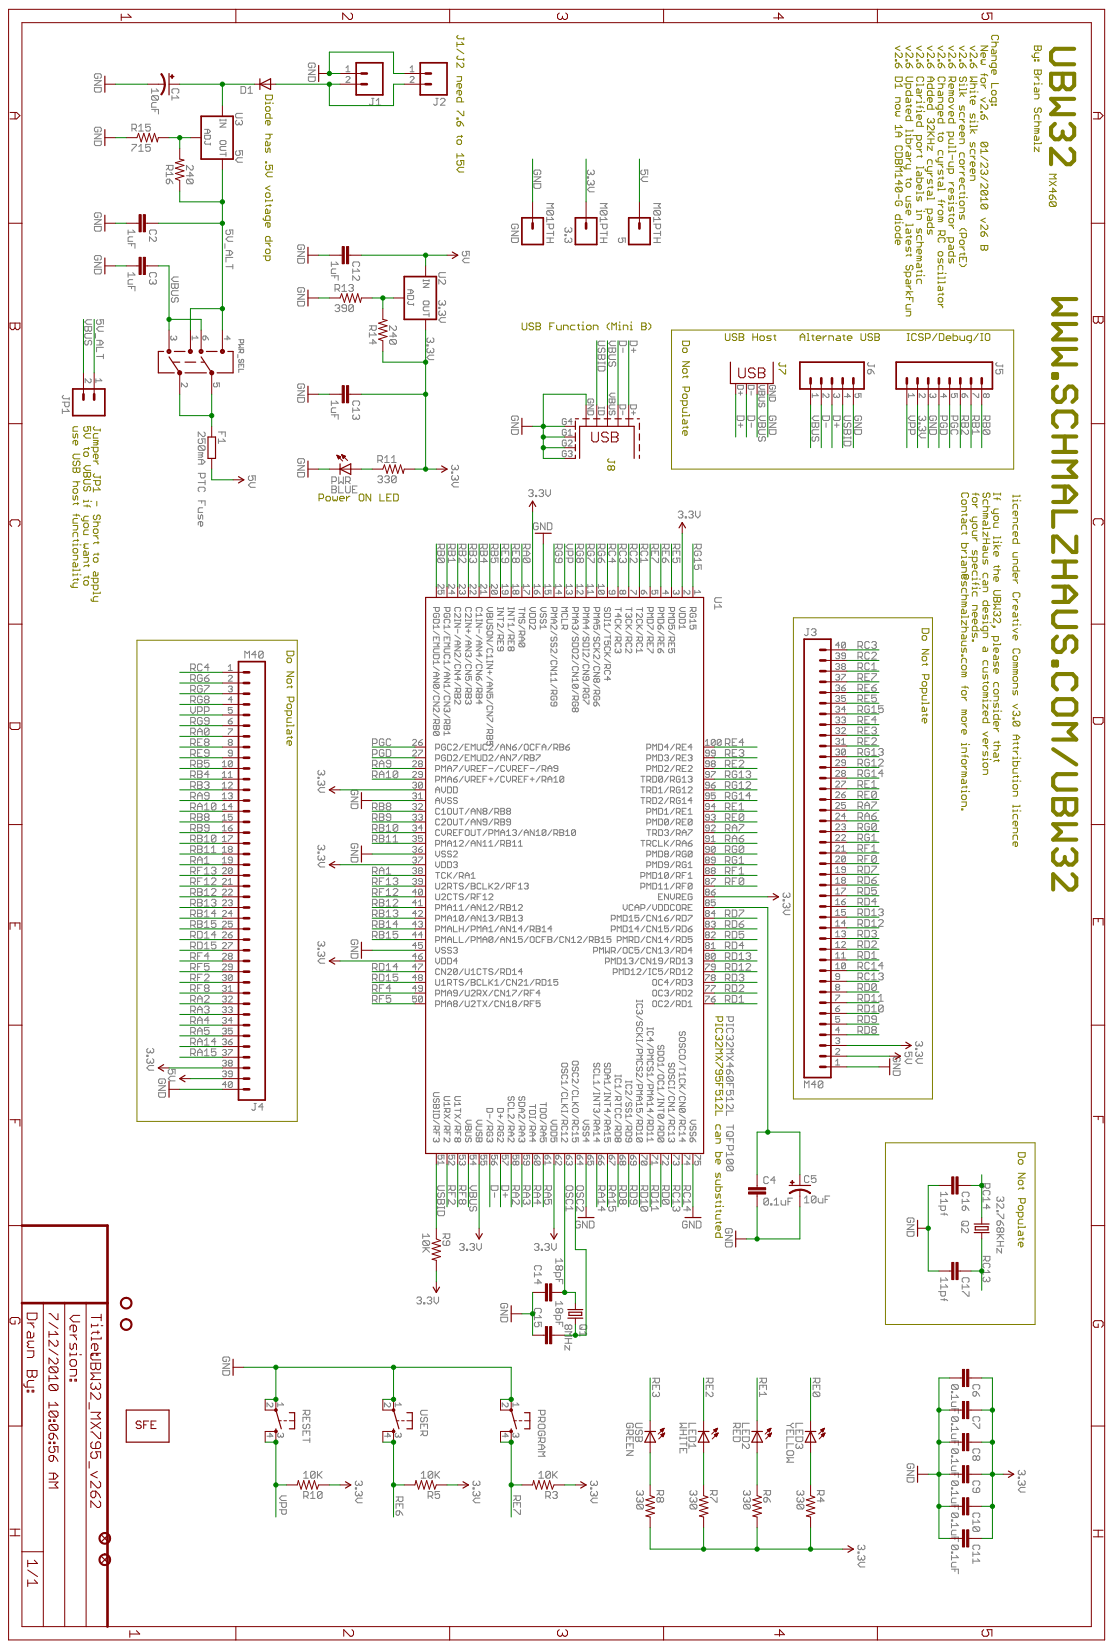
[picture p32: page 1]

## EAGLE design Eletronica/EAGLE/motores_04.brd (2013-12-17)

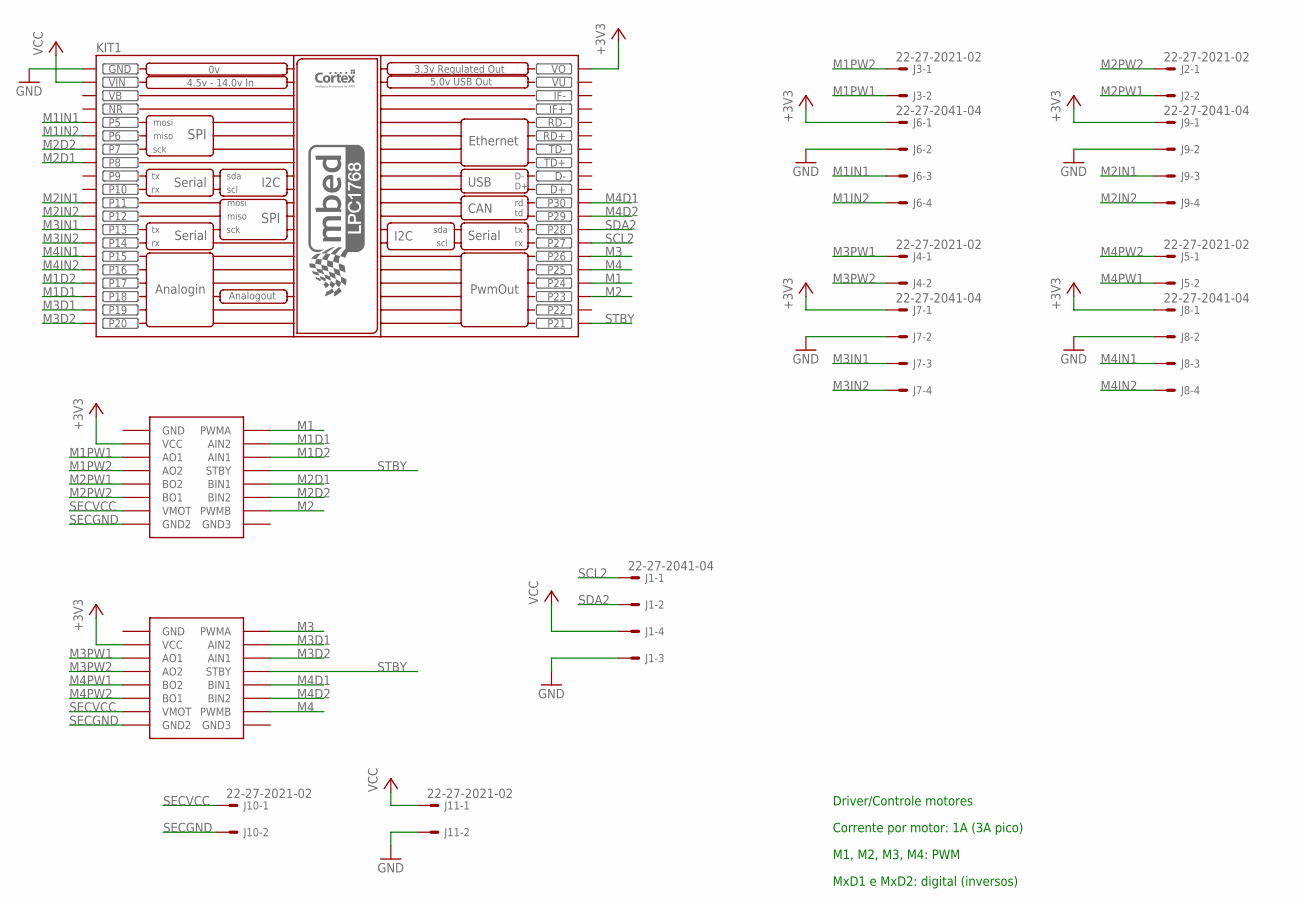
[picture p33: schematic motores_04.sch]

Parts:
J1, J6, J7, J8, J9: 22-27-2041-04; 6410-04
J2, J3, J4, J5, J10, J11: 22-27-2021-02; 6410-02
KIT1: MBED_NXP_LPC1768; MBED-KIT
U$1, U$2: MOTORDRIVER; 16PH

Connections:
+3V3: J6.1, J7.1, J8.1, J9.1, KIT1.VOUT (VO), U$1.P$2 (VCC), U$2.P$2 (VCC)
GND: J1.3, J6.2, J7.2, J8.2, J9.2, J11.2, KIT1.GND
M1: KIT1.P$24 (P24), U$1.P$16 (PWMA)
M1D1: KIT1.P$18 (P18), U$1.P$15 (AIN2)
M1D2: KIT1.P$17 (P17), U$1.P$14 (AIN1)
M1IN1: J6.3, KIT1.P$5 (P5)
M1IN2: J6.4, KIT1.P$6 (P6)
M1PW1: J3.2, U$1.P$3 (AO1)
M1PW2: J3.1, U$1.P$4 (AO2)
M2: KIT1.P$23 (P23), U$1.P$10 (PWMB)
M2D1: KIT1.P$8 (P8), U$1.P$12 (BIN1)
M2D2: KIT1.P$7 (P7), U$1.P$11 (BIN2)
M2IN1: J9.3, KIT1.P$11 (P11)
M2IN2: J9.4, KIT1.P$12 (P12)
M2PW1: J2.2, U$1.P$5 (BO2)
M2PW2: J2.1, U$1.P$6 (BO1)
M3: KIT1.P$26 (P26), U$2.P$16 (PWMA)
M3D1: KIT1.P$19 (P19), U$2.P$15 (AIN2)
M3D2: KIT1.P$20 (P20), U$2.P$14 (AIN1)
M3IN1: J7.3, KIT1.P$13 (P13)
M3IN2: J7.4, KIT1.P$14 (P14)
M3PW1: J4.1, U$2.P$3 (AO1)
M3PW2: J4.2, U$2.P$4 (AO2)
M4: KIT1.P$25 (P25), U$2.P$10 (PWMB)
M4D1: KIT1.P$30 (P30), U$2.P$12 (BIN1)
M4D2: KIT1.P$29 (P29), U$2.P$11 (BIN2)
M4IN1: J8.3, KIT1.P$15 (P15)
M4IN2: J8.4, KIT1.P$16 (P16)
M4PW1: J5.2, U$2.P$5 (BO2)
M4PW2: J5.1, U$2.P$6 (BO1)
NR: KIT1.NR
SCL2: J1.1, KIT1.P$27 (P27)
SDA2: J1.2, KIT1.P$28 (P28)
SECGND: J10.2, U$1.P$8 (GND2), U$2.P$8 (GND2)
SECVCC: J10.1, U$1.P$7 (VMOT), U$2.P$7 (VMOT)
STBY: KIT1.P$21 (P21), U$1.P$13 (STBY), U$2.P$13 (STBY)
VB: KIT1.VB
VCC: J1.4, J11.1, KIT1.VIN
VU: KIT1.VU

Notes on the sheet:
Driver/Controle motores
Corrente por motor: 1A (3A pico)
M1, M2, M3, M4: PWM
MxD1 e MxD2: digital (inversos)

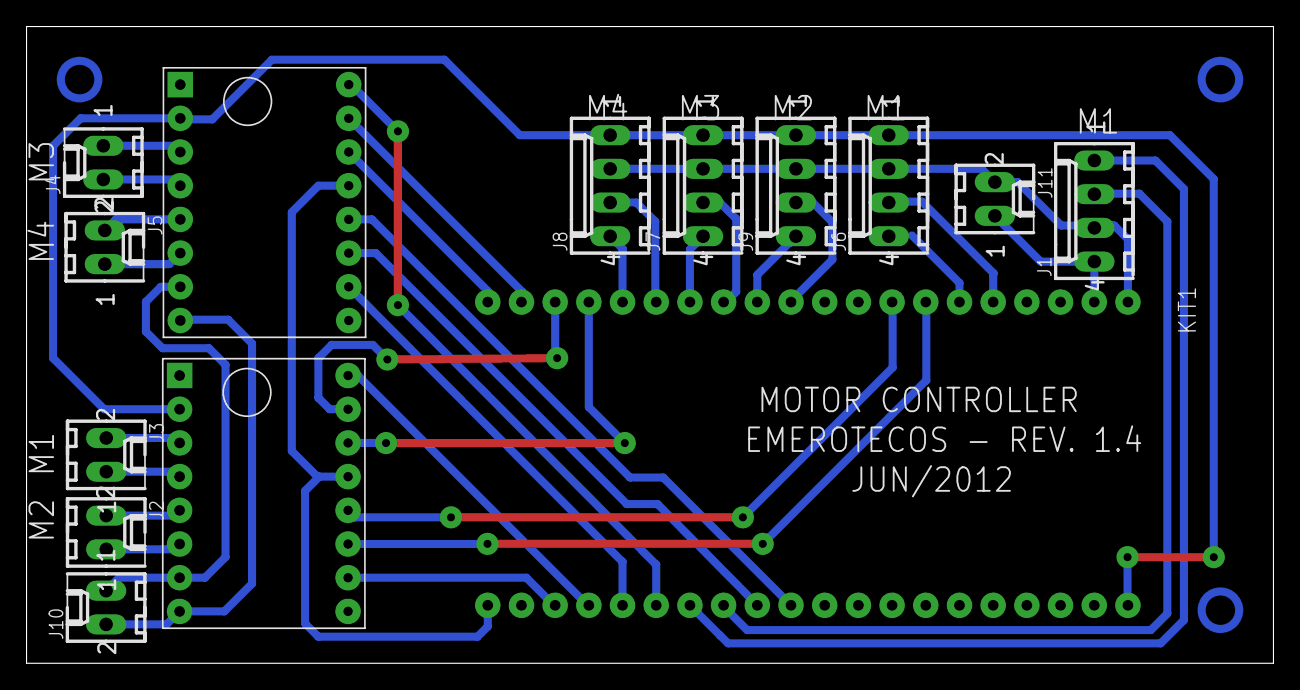
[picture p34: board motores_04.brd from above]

Board: 2 copper layers, 94.0 x 48.0 mm, 14 parts (0 on the bottom side), 36 nets.

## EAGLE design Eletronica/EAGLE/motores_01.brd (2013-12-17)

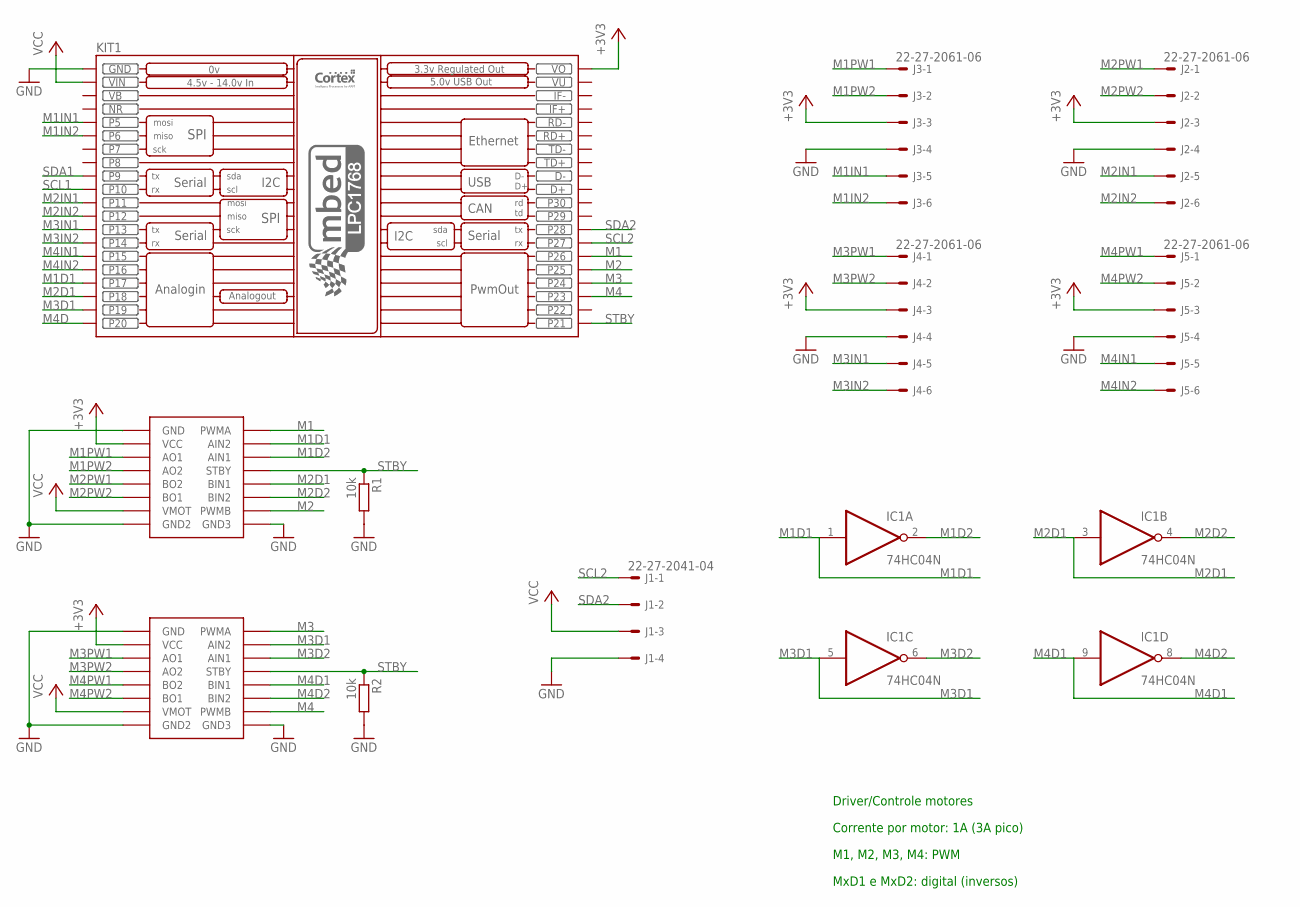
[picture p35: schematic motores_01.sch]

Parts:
IC1: 74HC04N; DIL14
J1: 22-27-2041-04; 6410-04
J2, J3, J4, J5: 22-27-2061-06; 6410-06
KIT1: MBED_NXP_LPC1768; MBED-KIT
R1, R2: 10k; 0204/7
U$1, U$2: MOTORDRIVER; 16PH

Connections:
+3V3: J2.3, J3.3, J4.3, J5.3, KIT1.VOUT (VO), U$1.P$2 (VCC), U$2.P$2 (VCC)
GND: IC1.7 (GND), J1.4, J2.4, J3.4, J4.4, J5.4, KIT1.GND, R1.2, R2.2, U$1.P$1 (GND), U$1.P$8 (GND2), U$1.P$9 (GND3), U$2.P$1 (GND), U$2.P$8 (GND2), U$2.P$9 (GND3)
M1: KIT1.P$26 (P26), U$1.P$16 (PWMA)
M1D1: IC1.1 (I), KIT1.P$17 (P17), U$1.P$15 (AIN2)
M1D2: IC1.2 (O), U$1.P$14 (AIN1)
M1IN1: J3.5, KIT1.P$5 (P5)
M1IN2: J3.6, KIT1.P$6 (P6)
M1PW1: J3.1, U$1.P$3 (AO1)
M1PW2: J3.2, U$1.P$4 (AO2)
M2: KIT1.P$25 (P25), U$1.P$10 (PWMB)
M2D1: IC1.3 (I), KIT1.P$18 (P18), U$1.P$12 (BIN1)
M2D2: IC1.4 (O), U$1.P$11 (BIN2)
M2IN1: J2.5, KIT1.P$11 (P11)
M2IN2: J2.6, KIT1.P$12 (P12)
M2PW1: J2.1, U$1.P$5 (BO2)
M2PW2: J2.2, U$1.P$6 (BO1)
M3: KIT1.P$24 (P24), U$2.P$16 (PWMA)
M3D1: IC1.5 (I), KIT1.P$19 (P19), U$2.P$15 (AIN2)
M3D2: IC1.6 (O), U$2.P$14 (AIN1)
M3IN1: J4.5, KIT1.P$13 (P13)
M3IN2: J4.6, KIT1.P$14 (P14)
M3PW1: J4.1, U$2.P$3 (AO1)
M3PW2: J4.2, U$2.P$4 (AO2)
M4: KIT1.P$23 (P23), U$2.P$10 (PWMB)
M4D: KIT1.P$20 (P20)
M4D1: IC1.9 (I), U$2.P$12 (BIN1)
M4D2: IC1.8 (O), U$2.P$11 (BIN2)
M4IN1: J5.5, KIT1.P$15 (P15)
M4IN2: J5.6, KIT1.P$16 (P16)
M4PW1: J5.1, U$2.P$5 (BO2)
M4PW2: J5.2, U$2.P$6 (BO1)
NR: KIT1.NR
SCL1: KIT1.P$10 (P10)
SCL2: J1.1, KIT1.P$27 (P27)
SDA1: KIT1.P$9 (P9)
SDA2: J1.2, KIT1.P$28 (P28)
STBY: KIT1.P$21 (P21), R1.1, R2.1, U$1.P$13 (STBY), U$2.P$13 (STBY)
VB: KIT1.VB
VCC: IC1.14 (VCC), J1.3, KIT1.VIN, U$1.P$7 (VMOT), U$2.P$7 (VMOT)
VU: KIT1.VU

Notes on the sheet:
Driver/Controle motores
Corrente por motor: 1A (3A pico)
M1, M2, M3, M4: PWM
MxD1 e MxD2: digital (inversos)

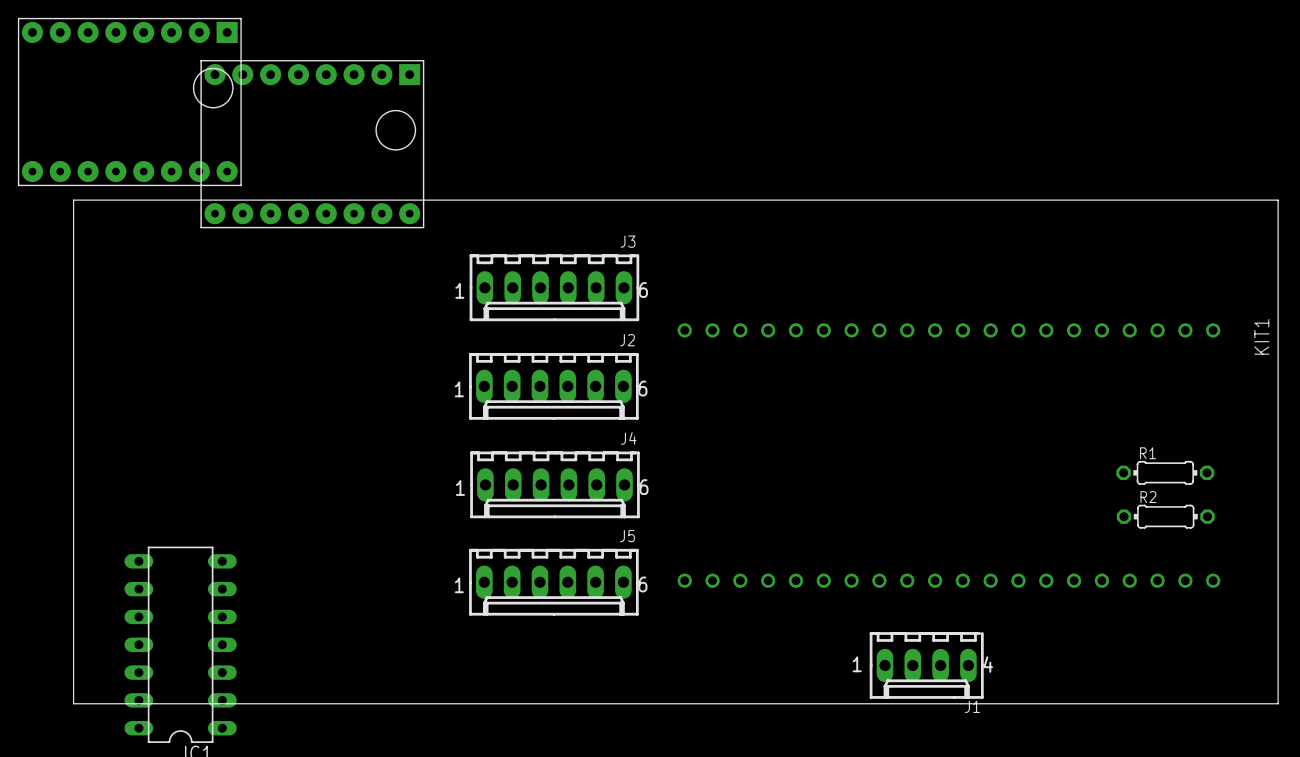
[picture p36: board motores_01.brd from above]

Board: 2 copper layers, 110.0 x 46.0 mm, 11 parts (0 on the bottom side), 34 nets.

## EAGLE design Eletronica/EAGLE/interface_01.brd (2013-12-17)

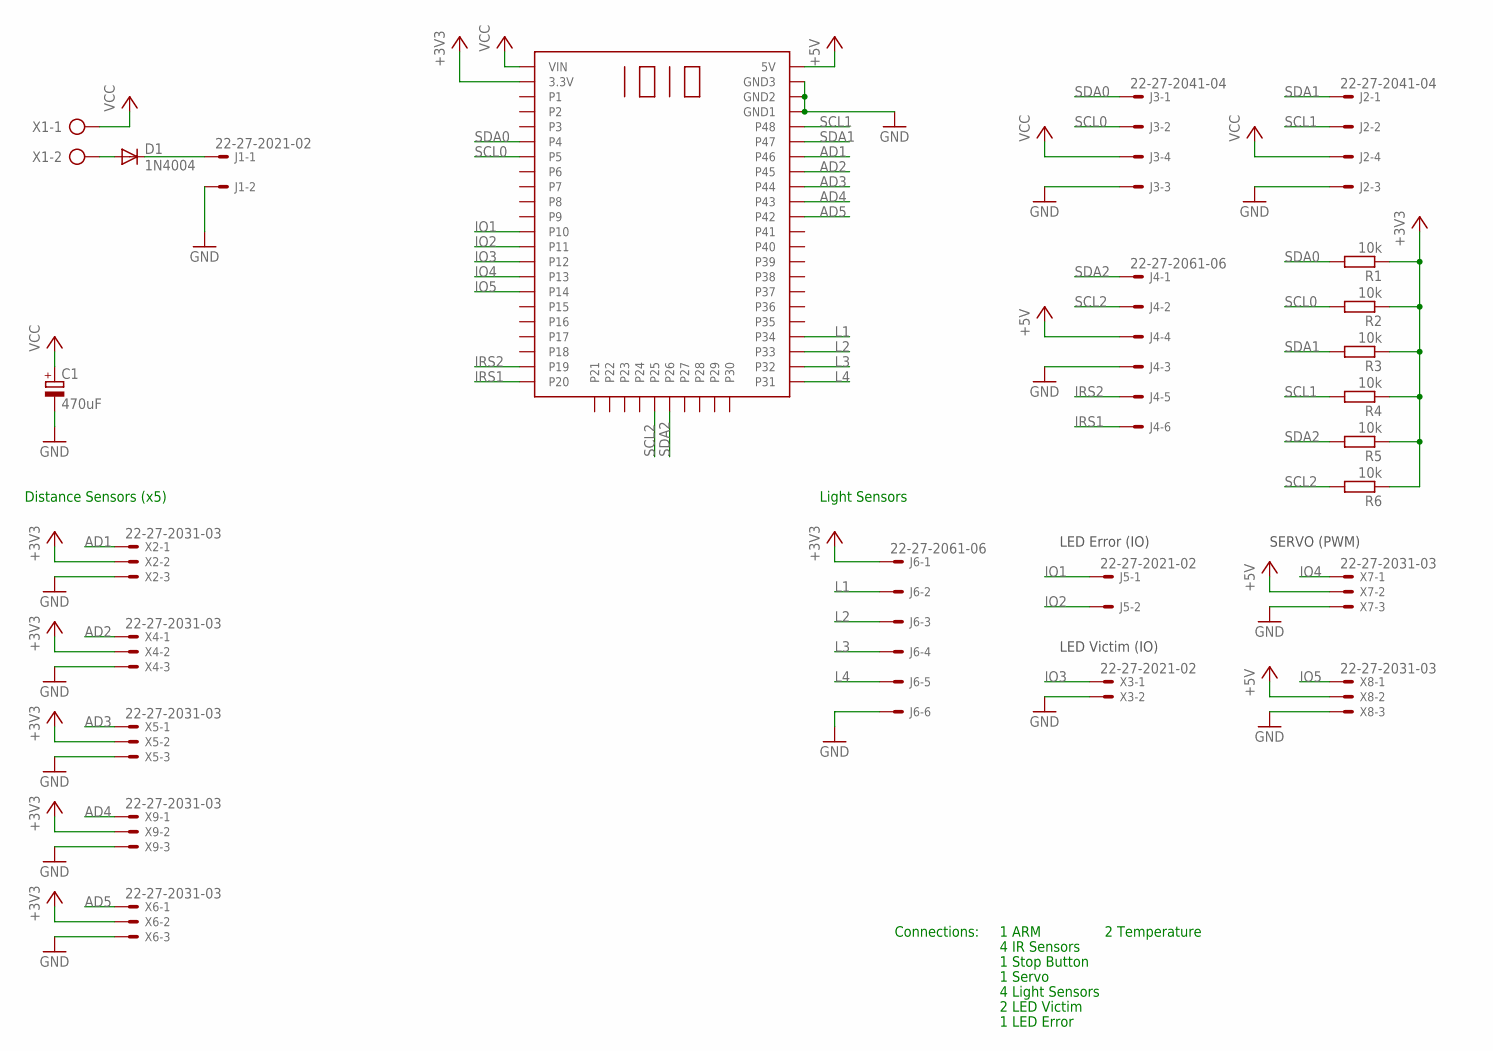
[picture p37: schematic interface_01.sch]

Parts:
C1: 470uF; E5-10,5
D1: 1N4004; DO41-10
J1, J5: 22-27-2021-02; 6410-02
J2, J3: 22-27-2041-04; 6410-04
J4, J6: 22-27-2061-06; 6410-06
R1, R2, R3, R4, R5, R6: 10k; 0204/7
U$1: IOIO
X1: AK500/2
X2, X4, X5, X6, X7, X8, X9: 22-27-2031-03; 6410-03
X3: 22-27-2021-02; 6410-02

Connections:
+3V3: J6.1, R1.1, R2.1, R3.1, R4.1, R5.1, R6.1, U$1.P$2 (3.3V), X2.2, X4.2, X5.2, X6.2, X9.2
AD1: U$1.P$48 (P46), X2.1
AD2: U$1.P$47 (P45), X4.1
AD3: U$1.P$46 (P44), X5.1
AD4: U$1.P$45 (P43), X9.1
AD5: U$1.P$44 (P42), X6.1
GND: C1.-, J1.2, J2.3, J3.3, J4.3, J6.6, U$1.P$51 (GND1), U$1.P$52 (GND2), U$1.P$53 (GND3), X2.3, X3.2, X4.3, X5.3, X6.3, X7.3, X8.3, X9.3
IO1: J5.1, U$1.P$12 (P10)
IO2: J5.2, U$1.P$13 (P11)
IO3: U$1.P$14 (P12), X3.1
IO4: U$1.P$15 (P13), X7.1
IO5: U$1.P$16 (P14), X8.1
IRS1: J4.6, U$1.P$22 (P20)
IRS2: J4.5, U$1.P$21 (P19)
L1: J6.2, U$1.P$36 (P34)
L2: J6.3, U$1.P$35 (P33)
L3: J6.4, U$1.P$34 (P32)
L4: J6.5, U$1.P$33 (P31)
unnamed: D1.A, X1.2
unnamed: D1.C, J1.1
unnamed: J4.4, U$1.P$54 (5V), X7.2, X8.2
SCL0: J3.2, R2.2, U$1.P$7 (P5)
SCL1: J2.2, R4.2, U$1.P$50 (P48)
SCL2: J4.2, R6.2, U$1.P$27 (P25)
SDA0: J3.1, R1.2, U$1.P$6 (P4)
SDA1: J2.1, R3.2, U$1.P$49 (P47)
SDA2: J4.1, R5.2, U$1.P$28 (P26)
VCC: C1.+, J2.4, J3.4, U$1.P$1 (VIN), X1.1

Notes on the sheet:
SERVO (PWM)
LED Error (IO)
LED Victim (IO)
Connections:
1 ARM
2 LED Victim
1 LED Error
1 Servo
4 Light Sensors
1 Stop Button
4 IR Sensors
2 Temperature
Distance Sensors (x5)
Light Sensors

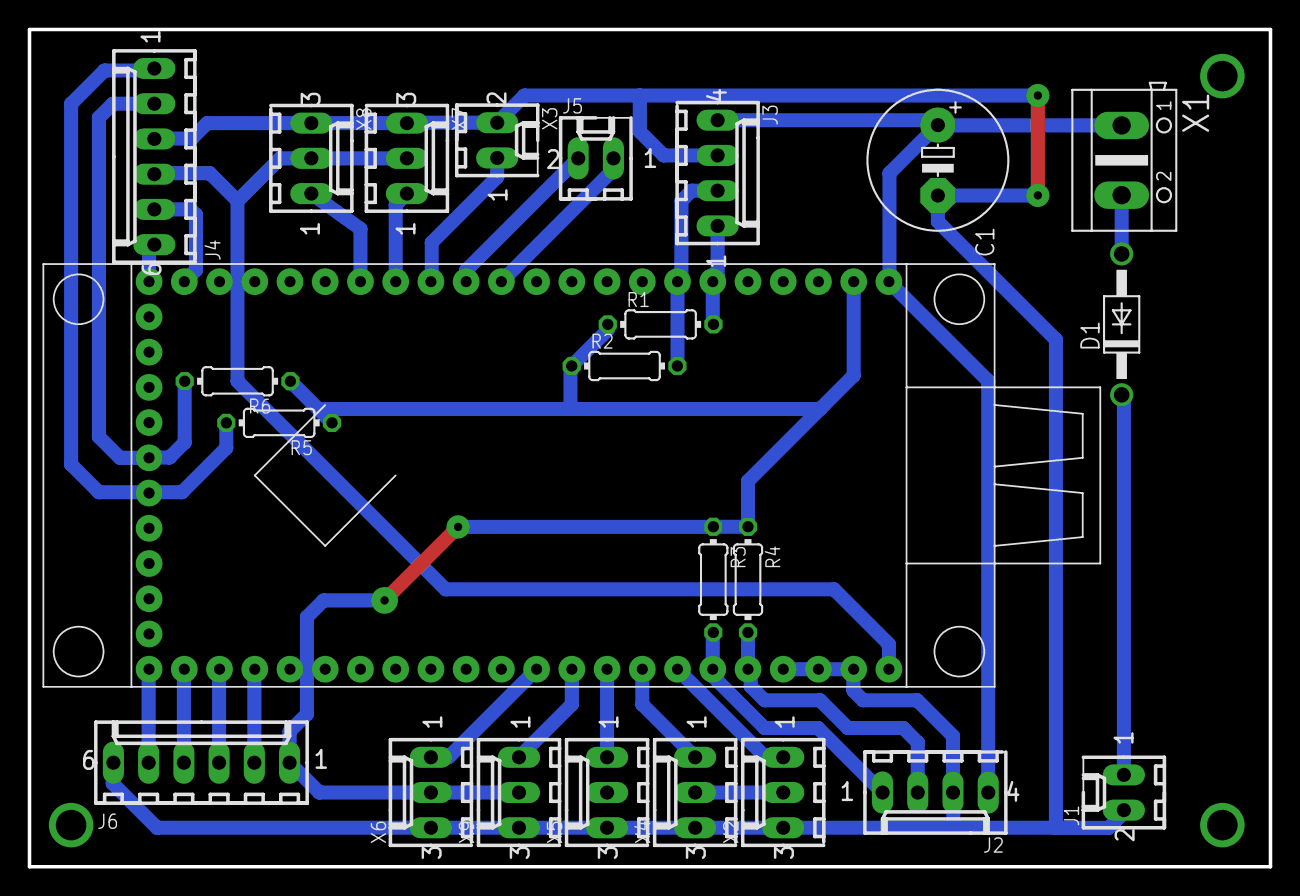
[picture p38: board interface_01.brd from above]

Board: 2 copper layers, 89.5 x 60.4 mm, 24 parts (0 on the bottom side), 28 nets.

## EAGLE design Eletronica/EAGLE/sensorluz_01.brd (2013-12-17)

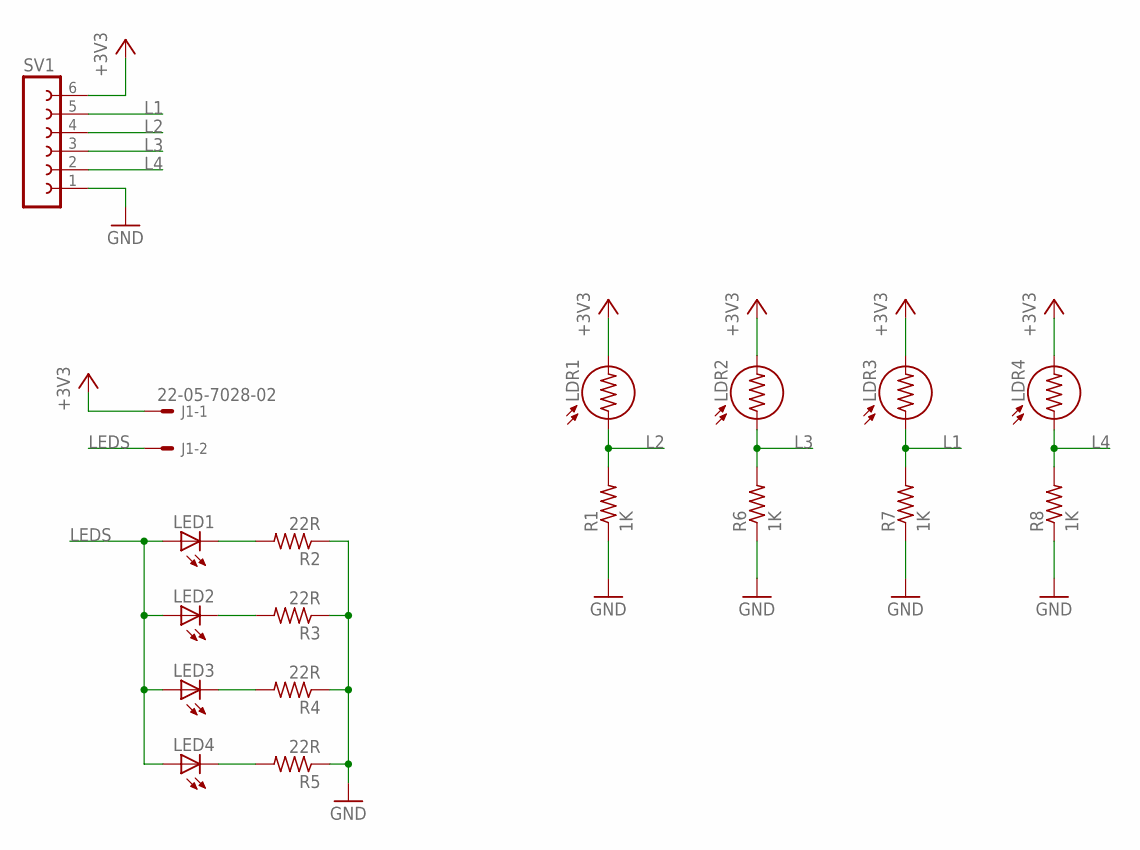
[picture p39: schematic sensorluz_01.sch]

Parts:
J1: 22-05-7028-02; 7395-02
LDR1, LDR2, LDR3, LDR4: LDR5MM; LDR338-54C
LED1, LED2, LED3, LED4: LED5MM
R1, R6, R7, R8: 1K; 0204/5
R2, R3, R4, R5: 22R; 0204/5
SV1: FE06W

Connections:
+3V3: J1.1, LDR1.2, LDR2.2, LDR3.2, LDR4.2, SV1.6
GND: R1.1, R2.1, R3.1, R4.1, R5.1, R6.1, R7.1, R8.1, SV1.1
L1: LDR3.1, R7.2, SV1.5
L2: LDR1.1, R1.2, SV1.4
L3: LDR2.1, R6.2, SV1.3
L4: LDR4.1, R8.2, SV1.2
LEDS: J1.2, LED1.A, LED2.A, LED3.A, LED4.A
unnamed: LED1.K (C), R2.2
unnamed: LED2.K (C), R3.2
unnamed: LED3.K (C), R4.2
unnamed: LED4.K (C), R5.2

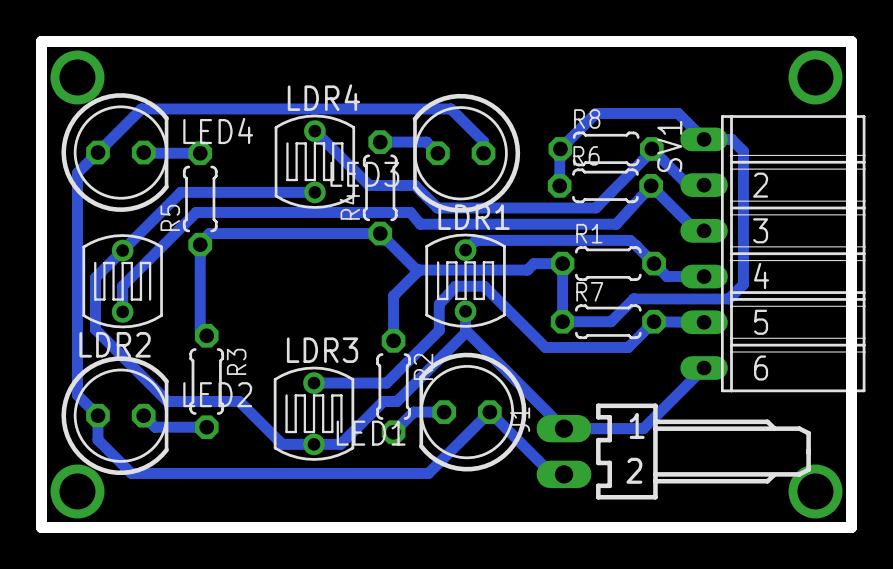
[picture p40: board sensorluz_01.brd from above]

Board: 2 copper layers, 45.0 x 27.0 mm, 18 parts (0 on the bottom side), 11 nets.

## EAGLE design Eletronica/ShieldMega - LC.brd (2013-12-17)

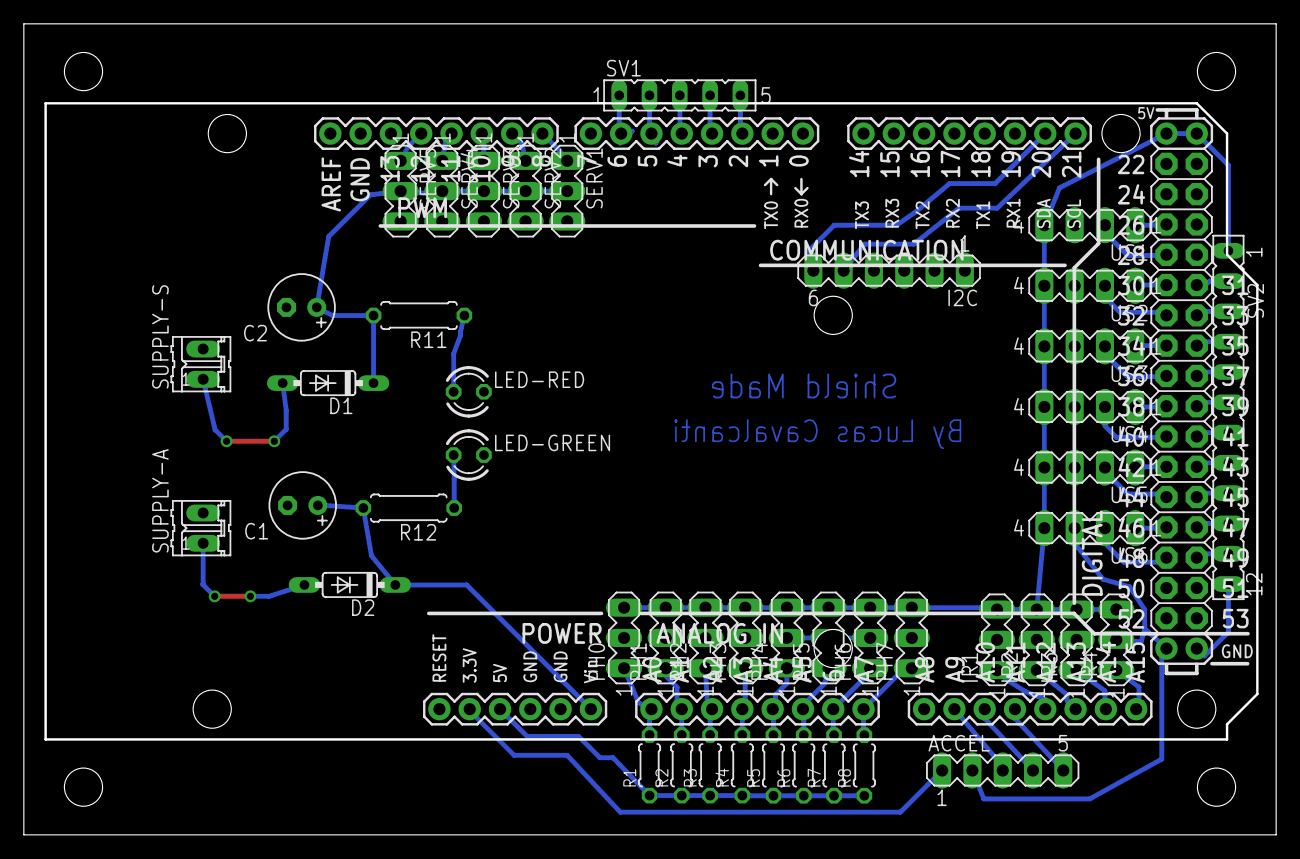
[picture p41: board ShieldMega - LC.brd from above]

Board: 2 copper layers, 105.0 x 68.0 mm, 46 parts (0 on the bottom side), 59 nets.

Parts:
ACCEL: MA05-1
C1, C2: E2,5-6
D1, D2: 1N4148DO35-7; DO35-7
I2C: MA06-1
IR1, IR2, IR3, IR4: MA03-1
LED-GREEN: LED3MM
LED-RED: LED3MM
PH0, PH1, PH2, PH3, PH4, PH5, PH6, PH7: MA03-1
R1, R2, R3, R4, R5, R6, R7, R8: 0204/5
R11, R12: 200; 0207/7
SERV1, SERV2, SERV3, SERV4, SERV5: MA03-1
SUPPLY-A: 02P
SUPPLY-S: 02P
SV1: FE05-1
SV2: FE12
U1: ARDUINO-MEGAFULL; ARDUINO_MEGA
US1, US2, US3, US4, US5, US6: MA04-1

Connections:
3V3: ACCEL.1, U1.3.3V
5V: R1.1, R2.1, R3.1, R4.1, R5.1, R6.1, R7.1, R8.1, U1.5V@0
5VU: IR1.3, IR2.3, IR3.3, IR4.3, PH0.3, PH1.3, PH2.3, PH3.3, PH4.3, PH5.3, PH6.3, PH7.3, SV2.1, U1.5V@1, U1.5V@2, US1.4, US2.4, US3.4, US4.4, US5.4, US6.4
31: SV2.2, U1.31
33: SV2.3, U1.33
35: SV2.4, U1.35
37: SV2.5, U1.37
39: SV2.6, U1.39
41: SV2.7, U1.41
43: SV2.8, U1.43
45: SV2.9, U1.45
47: SV2.10, U1.47
49: SV2.11, U1.49
A0: PH0.1, R1.2, U1.A0
A1: PH1.1, R2.2, U1.A1
A2: PH2.1, R3.2, U1.A2
A3: PH3.1, R4.2, U1.A3
A4: PH4.1, R5.2, U1.A4
A5: PH5.1, R6.2, U1.A5
A6: PH6.1, R7.2, U1.A6
A7: PH7.1, R8.2, U1.A7
ECHO1: U1.28, US1.2
ECHO2: U1.32, US2.2
ECHO3: U1.36, US3.2
ECHO4: U1.40, US4.2
ECHO5: U1.44, US5.2
ECHO6: U1.48, US6.2
GND: ACCEL.2, C1.-, C2.-, I2C.2, I2C.3, IR1.2, IR2.2, IR3.2, IR4.2, LED-GREEN.K, LED-RED.K, PH0.2, PH1.2, PH2.2, PH3.2, PH4.2, PH5.2, PH6.2, PH7.2, SERV1.3, SERV2.3, SERV3.3, SERV4.3, SERV5.3, SUPPLY-A.2, SUPPLY-S.2, SV2.12, U1.GND@0, U1.GND@1, U1.GND@2, U1.GND@3, U1.GND@4, US1.3, US2.3, US3.3, US4.3, US5.3, US6.3
IR1: IR1.1, U1.A12
IR2: IR2.1, U1.A13
IR3: IR3.1, U1.A14
IR4: IR4.1, U1.A15
unnamed: D2.A, SUPPLY-A.1
unnamed: SV1.5, U1.2
unnamed: D1.A, SUPPLY-S.1
unnamed: SV1.4, U1.3
unnamed: SV1.3, U1.4
unnamed: SV1.2, U1.5
unnamed: SV1.1, U1.6
unnamed: LED-GREEN.A, R12.1
unnamed: LED-RED.A, R11.1
PWM1: SERV1.1, U1.8
PWM2: SERV2.1, U1.9
PWM3: SERV3.1, U1.10
PWM4: SERV4.1, U1.11
PWM5: SERV5.1, U1.12
SCL: I2C.5, U1.21
SDA: I2C.6, U1.20
TRIG1: U1.26, US1.1
TRIG2: U1.30, US2.1
TRIG3: U1.34, US3.1
TRIG4: U1.38, US4.1
TRIG5: U1.42, US5.1
TRIG6: U1.46, US6.1
VIN-A: C1.+, D2.C, R12.2, U1.VIN
VIN-S: C2.+, D1.C, R11.2, SERV1.2, SERV2.2, SERV3.2, SERV4.2, SERV5.2
X: ACCEL.3, U1.A9
Y: ACCEL.4, U1.A10
Z: ACCEL.5, U1.A11

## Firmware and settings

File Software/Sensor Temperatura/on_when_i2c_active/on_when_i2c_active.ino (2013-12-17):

/*
  Blink
  Turns on an LED on for one second, then off for one second, repeatedly.
 
  This example code is in the public domain.
 */
int led = 8;
int i2c = A5;

void setup() {                
  // initialize the digital pin as an output.
  // Pin 13 has an LED connected on most Arduino boards:
  pinMode(led, OUTPUT);     
  pinMode(stat, INPUT);     
}

void loop() {
  if(digitalRead(stat) == LOW){
    digitalWrite(pin, HIGH);   // set the LED on
    delay(50);              // wait for a second
    digitalWrite(pin, LOW);    // set the LED off
  }
}

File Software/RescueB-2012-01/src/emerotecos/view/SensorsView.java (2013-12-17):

package emerotecos.view;

import java.util.ArrayList;

import android.content.Context;
import android.graphics.Bitmap;
import android.graphics.BitmapFactory;
import android.graphics.Canvas;
import android.graphics.Color;
import android.graphics.Paint;
import android.graphics.Paint.Style;
import android.graphics.Path;
import android.graphics.Point;
import android.util.AttributeSet;
import android.view.MotionEvent;
import android.view.View;
import emerotecos.rescue.b.Program1.State;
import emerotecos.rescue.b.R;
import emerotecos.rescue.b.RobotActivity;
import emerotecos.util.BaseRescueBLooper;
import emerotecos.util.Cell;
import emerotecos.util.IRDistanceSensor;
import emerotecos.util.Map;
import emerotecos.util.MapController;
import emerotecos.util.ServoController;
import emerotecos.util.Statable;
import emerotecos.util.Wall;

public class SensorsView extends View {
	
	/*
	 * FUNCTIONALITY OBJECTS
	 */
	BaseRescueBLooper Robot;
	ArrayList<IRDistanceSensor> DistanceSensors;
	double[] DistanceSensorsAngle = {0, 0, 0, 0};
	ServoController servo;	
	
	/*
	 * Maps
	 */
	MapController mapController = null;

	/*
	 * SCALES
	 */
	public final static double DistSCALE  = 4;
	public final static double WallDist	= 30;
	
	/*
	 * POSITIONING AND ANGLE ATRIBUTES
	 */
	int xPos = 0, yPos = 0;
	
	/*
	 * DRAWING OBJECTS
	 */
	Paint pDistanceSensor;
	Paint pRoute;
	Paint pText;
	Paint pTextError;
	Paint pTextVictim;
	Paint pFillRed;
	Paint pWallClear;
	Paint pWallExist;
	Paint pCellVisited;
	Paint pCellClear;
	Paint pCellVictim;
	Paint pTextVictimBg;
	Paint pCellBlack;

	public void setPosition(int x, int y){
		xPos = x;
		yPos = y;
	}
	
	public Statable robotState = null;
	
	public double getRobotAngleRad(){
		//int angle = mapController.dir.getValue()*90 + 180;
		int angle = mapController.dir.getValue()*90 + 180;
		return Math.toRadians(angle);
	}
	public double getHeadAngleRad(){
		int angle = (servo.getPosition())*-1 - 90;
		return Math.toRadians(angle)-getRobotAngleRad();
	}
	
	public ArrayList<Point> path = null;
	Path route = new Path();
	protected void drawPath(Canvas canvas, int xOffset, int yOffset){
		
		if(path != null){
			if(path.size() > 0){
				int x, y;
				boolean first = true;
				route.reset();
				for(Point a: path){
					x = (int) (a.x*WallDist*DistSCALE + WallDist*DistSCALE/2);
					y = (int) (a.y*WallDist*DistSCALE*-1 - WallDist*DistSCALE/2);
					 
					if(first){
						route.setLastPoint(x, y);
						first = false;
					}else{
						route.lineTo(x, y);
					}
				}
				//route.close();
				canvas.save();
				canvas.translate(xPos+xOffset, yPos+yOffset);
				canvas.drawPath(route, pRoute);
				canvas.restore();
				
				canvas.drawText("Path len.: "+path.size(),10, 220, pText);
			}else{
				canvas.drawText("Path is empty!",10, 220, pTextError);
			}
		}else{
			canvas.drawText("Path is not inited!",10, 220, pTextError);
		}
		
	}
	
	Bitmap rawRobot;
	Bitmap robot;
	protected void drawRobot(Canvas canvas, int xOffset, int yOffset){
		canvas.save();
		canvas.rotate(mapController.dir.getValue()*90 + 180, xPos+xOffset, yPos+yOffset);
		canvas.save();
		canvas.translate(xPos+xOffset, yPos+yOffset);
		canvas.drawPath(arrow, pFillRed);
		canvas.restore();
		canvas.restore();
	}
	protected void drawSensors(Canvas canvas, int xOffset, int yOffset){
		double tmp_angle = getHeadAngleRad();
		double tmp_distance;
		
		//Matrix robotM = new Matrix();
		//robot = Bitmap.createScaledBitmap(rawRobot, 86, 86, true);
		//robotM.setRotate(mapController.getHeading()+45);
		//canvas.drawBitmap(Bitmap.createBitmap(robot, 0, 0, robot.getWidth(), robot.getHeight(), robotM, true),xPos + xOffset -43,yPos + yOffset - 43, pText);
		for(int i = 0; i < 4; i++){
			tmp_distance = DistanceSensors.get(i).lastMeasure;
			//if(tmp_distance < 60){
				canvas.drawText("D"+(i+1)+": "+Math.round(tmp_distance) , 10+(i*100)%200, (i < 2? 40: 80), pText);
				
				canvas.drawLine(
					xOffset+xPos,
					yOffset+yPos,
					(int)(Math.sin(tmp_angle+DistanceSensorsAngle[i])*DistSCALE*tmp_distance)
						+xOffset+xPos,
					(int)(Math.cos(tmp_angle+DistanceSensorsAngle[i])*DistSCALE*tmp_distance)
						+yOffset+yPos,
					pDistanceSensor);
			//}
		}
		canvas.drawText("Servo angle: "+Robot.servo.getPosition(),10, 120, pText);
		canvas.drawText("RobotAngle: "+(mapController.dir.getValue()*90+180)%360,10, 160, pText);
	}
	
	float xS, xE, yS, yE;
	Cell cell_tmp;
	protected void drawMap(Canvas canvas, double xOffset, double yOffset){
		if(mapController != null){
			// Render Map
			Map map = mapController.map;
			
			for(int x = 0; x < 10; x++){
				for(int y = 0; y < 5; y++){
					xS = (float) (x*WallDist*DistSCALE + xOffset + xPos);
					xE = (float) ((x+1)*WallDist*DistSCALE + xOffset + xPos);
					yS = (float) (y*WallDist*DistSCALE*-1 + yOffset + yPos);
					yE = (float) ((y+1)*WallDist*DistSCALE*-1 + yOffset + yPos);
					cell_tmp = map.getCell(x, y);
					
					if(cell_tmp.hasVictim){
						canvas.drawRect(xS, yS, xE, yE, pCellVictim);
					}else if(cell_tmp.isBlack){
						canvas.drawRect(xS, yS, xE, yE, pCellBlack);
					}else if(cell_tmp.isVisited){
						canvas.drawRect(xS, yS, xE, yE, pCellVisited);
					}else{
						canvas.drawRect(xS, yS, xE, yE, pCellClear);
					}
					
					// North Wall
					if(cell_tmp.WallNorth.getStatus() == Wall.wUnknown)
						canvas.drawLine(xS, yE, xE, yE, pWallClear);
					else if(cell_tmp.WallNorth.getStatus() == Wall.wExist)
						canvas.drawLine(xS, yE, xE, yE, pWallExist);
					// South Wall
					if(cell_tmp.WallSouth.getStatus() == Wall.wUnknown)
						canvas.drawLine(xS, yS, xE, yS, pWallClear);
					else if(cell_tmp.WallSouth.getStatus() == Wall.wExist)
						canvas.drawLine(xS, yS, xE, yS, pWallExist);
					// West Wall
					if(cell_tmp.WallWest.getStatus() == Wall.wUnknown)
						canvas.drawLine(xS, yS, xS, yE, pWallClear);
					else if(cell_tmp.WallWest.getStatus() == Wall.wExist)
						canvas.drawLine(xS, yS, xS, yE, pWallExist);
					
					// East Wall
					if(cell_tmp.WallEast.getStatus() == Wall.wUnknown)
						canvas.drawLine(xE, yS, xE, yE, pWallClear);
					else if(cell_tmp.WallEast.getStatus() == Wall.wExist)
						canvas.drawLine(xE, yS, xE, yE, pWallExist);
					
					canvas.drawText("("+x+","+y+")", xS+30, yS-40, pText);
				}
			}
			if(mapController.getThisCell().hasVictim){
				canvas.drawRect(0, 0, canvas.getWidth(), canvas.getHeight(), pTextVictimBg);
				canvas.drawText("VICTIM", 50, 300, pTextVictim);
			}
		}
	}
	
	/* Current x and y of the touch */
	private float mCurrentX = 0;
	private float mCurrentY = 0;
	 
	/* The touch distance change from the current touch */
	private float mDeltaX = 0;
	private float mDeltaY = 0;
	
	public boolean dragable = false;
	
	@Override
	public boolean onTouchEvent(MotionEvent event) {
		if(dragable){
			if (event.getAction() == MotionEvent.ACTION_DOWN) {
				mCurrentX = event.getRawX();
				mCurrentY = event.getRawY();
				mDeltaX = 0;
				mDeltaY = 0;
			}
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

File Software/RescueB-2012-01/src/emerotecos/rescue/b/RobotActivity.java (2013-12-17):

package emerotecos.rescue.b;

import ioio.lib.util.android.IOIOActivity;
import android.app.ActionBar;
import android.content.Context;
import android.hardware.Sensor;
import android.hardware.SensorEvent;
import android.hardware.SensorEventListener;
import android.hardware.SensorManager;
import android.os.Bundle;
import android.os.Handler;
import android.util.Log;
import android.view.Menu;
import android.view.MenuInflater;
import android.view.MenuItem;
import android.view.WindowManager;

public class RobotActivity extends IOIOActivity implements IOIOEvents, SensorEventListener {
	protected Handler handler = new Handler();
	protected ActionBar actbar;
	protected Menu menu;

	//public static boolean isConnected = false;
	
	/*
	 * Android SENSORS
	 */
	public static SensorManager sensorManager;
	public static Sensor accellSensor;
	public static float[] accellVals = {0,0,0};
	
	public static Sensor angleSensor;
	public static float[] angleVals = {0,0,0};
	
	public static Sensor gyroSensor;
	public static float[] gyroVals = {0,0,0};
	public static double[] gyroIntVals = {0,0,0};
	
	public static void resetOnRamp(){
		gyroIntVals[1] = 0;
	}
	public static boolean isOnRamp(){
		
		if(Math.abs(gyroIntVals[1]) < 13){
			return false;
		}else{
			return true;
		}
		
	}
	
	public MenuItem ioio_status;
	public MenuItem robot_status;
	public MenuItem servo_status;
	
	@Override
	public void onCreate(Bundle savedInstanceState) {
		// Configure Android Sensors
		sensorManager = (SensorManager)getSystemService(Context.SENSOR_SERVICE);
		angleSensor = sensorManager.getDefaultSensor(Sensor.TYPE_ORIENTATION);
		accellSensor = sensorManager.getDefaultSensor(Sensor.TYPE_ACCELEROMETER);
		gyroSensor = sensorManager.getDefaultSensor(Sensor.TYPE_GYROSCOPE);
		super.onCreate(savedInstanceState);
		//setContentView(R.layout.main);

		actbar = this.getActionBar();
		actbar.setDisplayShowTitleEnabled(false);
		
		getWindow().addFlags(WindowManager.LayoutParams.FLAG_KEEP_SCREEN_ON);
	}
	
	@Override
	protected void onPause() {
	    // Unregister the listener on the onPause() event to preserve battery life;
	    super.onPause();
	    sensorManager.unregisterListener(this);
	    Log.i("RescueB.RobotActivity", "Sensors Listners removed");
	}

	@Override
	protected void onResume() {
	    super.onResume();
	    //sensorManager.registerListener(this, accellSensor, SensorManager.SENSOR_DELAY_GAME);
	    sensorManager.registerListener(this, gyroSensor, SensorManager.SENSOR_DELAY_GAME);
	    Log.i("RescueB.RobotActivity", "Sensors Listners added");
	}
	
	// IOIO Methods
	public void notifyIOIOhasConnected() {
		handler.post(new Runnable() {

			public void run() {
				ioio_status.setIcon(R.drawable.ioio_connected);
				robot_status.setVisible(true);
			}
		});
		//isConnected = true;
	}

	public void notifyIOIOhasDisconnected() {
		handler.post(new Runnable() {

			public void run() {
				if(ioio_status != null){
					ioio_status.setIcon(R.drawable.ioio_disconnected);
					robot_status.setVisible(false);
				}
			}
		});
		//isConnected = false;
	}

	public void changeRobotStatusIcon(final int Drawable){
		handler.post(new Runnable() {

			public void run() {
				if(robot_status != null)
					robot_status.setIcon(Drawable);
			}
		});
	}
	
	public boolean onCreateOptionsMenu(Menu menu) {
		MenuInflater inflater = getMenuInflater();
		inflater.inflate(R.menu.main, menu);
		
		ioio_status = (MenuItem) menu.findItem(R.id.ioio_status);
		ioio_status.setEnabled(false);
		ioio_status.setIcon(R.drawable.ioio_disconnected);
		
		robot_status = (MenuItem) menu.findItem(R.id.robot_status);
		robot_status.setEnabled(false);
		
		/*servo_status = (MenuItem) menu.findItem(R.id.servo_status);
		servo_status.setIcon(R.drawable.refresh);
		servo_status.setEnabled(false);
		*/
		this.menu = menu;
		
		return true;
	}

	// Sensors Listners
	public void onAccuracyChanged(Sensor sensor, int accuracy) {
	}

	public long lastGyro = System.nanoTime();
	//long nowGyro, delta;
	public double k = 1.15385;
	public void onSensorChanged(SensorEvent event) {
		if(event.sensor == angleSensor){
			angleVals[0] = event.values[0];
			angleVals[1] = event.values[1];
			angleVals[2] = event.values[2];
		}else if(event.sensor == accellSensor){
			accellVals[0] = event.values[0];
			accellVals[1] = event.values[1];
			accellVals[2] = event.values[2];
		}else if(event.sensor == gyroSensor){
			gyroVals[0] = event.values[0];
			gyroVals[1] = event.values[1];
			gyroVals[2] = event.values[2];
			
			/*nowGyro = System.nanoTime();
			delta = nowGyro - lastGyro;
			lastGyro = nowGyro;*/
			gyroIntVals[0] += /*delta */ gyroVals[0] * k;
			gyroIntVals[1] += /*delta */ gyroVals[1] * k;
			gyroIntVals[2] += /*delta */ gyroVals[2] * k;
		}
		//Log.i("RescueB.RobotActivity", "New samples from sensor!");
	}
}

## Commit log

2013-12-17 Electronics upload
    [IOIO-v15.brd, IOIO-v15.sch, Interface.sch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]
2013-12-17 Mechanics upload
    [Base_sensor_luz.DXF, Base_sensor_luz.SLDDRW, Base_sensor_luz.SLDPRT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]
2013-12-17 Research and test files
    [Testes_inercia.xlsx, degrees_10.csv, degrees_11.csv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]
2013-12-17 Software upload
    [proguard.cfg]

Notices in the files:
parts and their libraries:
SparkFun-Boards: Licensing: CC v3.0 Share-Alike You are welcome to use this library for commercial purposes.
